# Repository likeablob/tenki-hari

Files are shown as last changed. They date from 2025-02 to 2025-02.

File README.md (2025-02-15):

<div align="center">
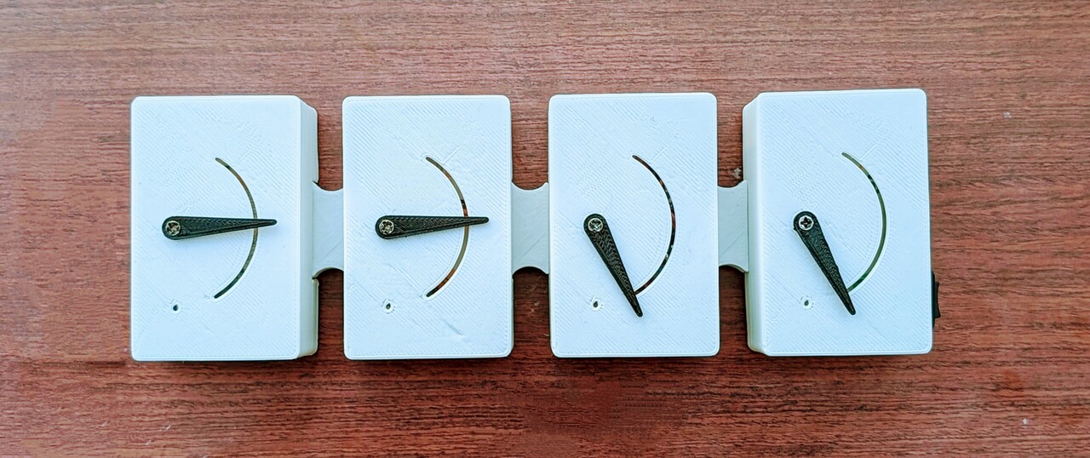
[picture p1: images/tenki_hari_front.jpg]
  
</div>

# Tenki Hari (Weather Needles, *ja: 天気針*)

A minimal weather forecast display gadget – and an experiment in building a battery-powered IoT device with [ESPHome](https://esphome.io/).

## Intro: How I Learned to Stop Worrying and Love ESPHome

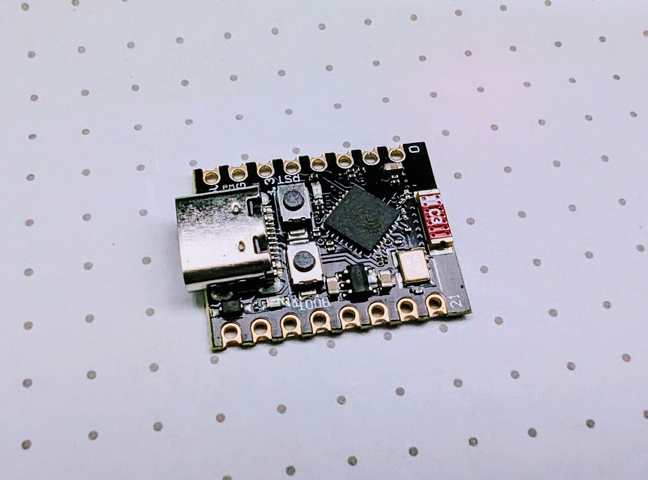
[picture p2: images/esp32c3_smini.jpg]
ESP32-C3 Super Mini


Building home IoT gadgets with embedded programming is fun. However, keeping track of devices scattered around the house ("What *was* that hostname?"), managing over-the-air software updates, and integrating with Home Assistant... not so much.

That's where ESPHome comes in. Think of it as Ansible or Kubernetes for ESP microcontrollers (beware, there's a lot of explicit YAML contents ahead).  It's somewhat similar to [Tasmota](https://tasmota.github.io/docs/), but in my experience, Tasmota is more focused on being an alternative firmware for ESP-based IoT devices.  
ESPHome, while it can certainly be used that way, really shines when it comes to customization.

Here's what I like about ESPHome:

- **Multiple flashing methods supported:** USB, Web Serial!, OTA, via Web UI, and even a full-featured **CLI**.
  - You can even see `ESP_LOGD()` logs over the air.
- **YAML-based device definitions:** (Yes, it's a paved road to YAML HELL.  Keep it simple, stupid!)
  - Secret management using `include` YAMLs (about as good as a `.gitignore`-ed `config.h`).
  - Config validation and autocompletion, thanks to the defined schema.
- **Simple device management dashboard::** Again, CLI is supported, meaning it works headless.
- **Automatic Home Assistant integration:** Devices are auto-detected with HA entities.
- **Extensive peripheral/external device support:** e.g., SPI/I2C sensors, etc.

For example, add this to your device's YAML and flash:

```sh
switch:
  - platform: gpio
    name: "Charge Port 1"
    pin: GPIO4
    restore_mode: RESTORE_DEFAULT_ON
```

Voila! Before you can even finish sipping your coffee, a switch entity appears in your Home Assistant instance.



Sure, it takes away some of the coding fun. However, you can still inject C++ snippets using the [`lambda:` syntax](https://esphome.io/cookbook/lambda_magic.html).  Black magic?  Maybe.  ESPHome is also can be considered as a wrapper that generates Arduino or esp-idf based firmware from your YAML definitions.

## Installation (Quick Overview)

The official ESPHome [Getting Started](https://esphome.io/guides/getting_started_command_line) guide covers installation, but in my case, it was as simple as adding 10 lines to my Home Assistant `docker-compose.yaml`:

```yaml
  esphome:
    container_name: esphome
    image: ghcr.io/esphome/esphome:2024.12.4
    volumes:
      - ./esphome/config:/config
      - /etc/localtime:/etc/localtime:ro
    restart: always
    privileged: true
    network_mode: host # For mDNS
    env_file:
      - esphome.env # This contains `USERNAME` and `PASSWORD`
```

Then, just navigated to http://localhost:6052, clicked `NEW DEVICE`, and followed the wizard. ESPHome creates a `<device-name>.yaml` file to your local filesystem, which you can edit via the dashboard and update via `Install > Wirelessly`.

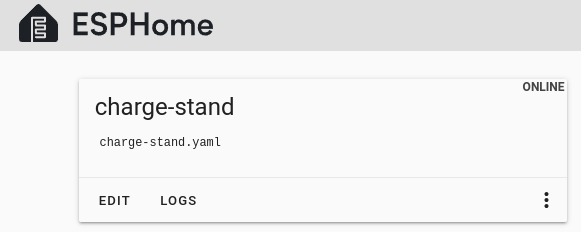
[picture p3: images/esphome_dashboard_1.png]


With this setup, you also need to register the device with Home Assistant for the first time.  When the device is discovered in "Integrations," copy and paste the API key from ESPHome.

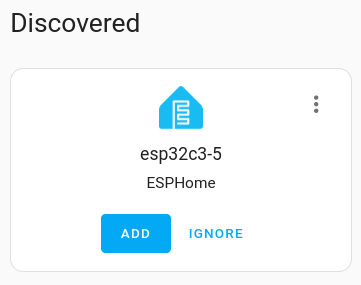
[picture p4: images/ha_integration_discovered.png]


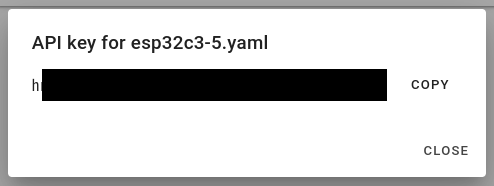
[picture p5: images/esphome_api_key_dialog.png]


One quick note: for initial flashing via the dashboard (using Web Serial), you'll need `localhost` or `https://`. SSH port forwarding (`-L 6052:localhost:6052`) to your home lab server, or you can set up HTTPS with Caddy or Tailscale.  Alternatively, use the [ESPHome Flasher](https://web.esphome.io/) or the CLI (`docker compose exec esphome`).

### Building a Battery-Powered Device with ESPHome

I've built several battery-powered devices in the past, primarily using Arduino ([1](https://github.com/likeablob/slow-movie-player-7c), [2](https://hackaday.io/project/184009-endless-endless-eight)).  Could I build something similar with ESPHome? (Spoiler: Yes!)

Here's the goal:

- An ESP32-C3 powered by 4 x NiMH AA batteries, lasting for *at least* 6 months.
- Wakes up hourly, retrieves the weather forecast for a few hours ahead, and moves a servo to indicate the conditions.
- Wakes up at *specific* times (not just periodically), like 5 minutes past the hour, every hour (`5 * * * *`).

```mermaid
gantt
    dateFormat  HH:mm
    axisFormat  %H:%M
    title       Device sleep and wake schedule

    section Home Assistant
        Fetch weather forecast : milestone, m1, 01:00, 1m
        Fetch weather forecast : milestone, m2, 02:00, 1m
        Fetch weather forecast : milestone, m2, 03:00, 1m

    section Device
        Boot       : milestone, crit, w1, 00:55, 0.2m
        Sleep      : done, after w1, 10m
        Wake       : crit, w2, 01:05, 0.2m
        Sleep      : done, after w2, 59.8m
        Wake       : crit, w3, 02:05, 0.2m
        Sleep      : done, after w3, 59.8m
```

First, [deep sleep is supported](https://esphome.io/components/deep_sleep).  However, by default, ESPHome [provides an API on the device itself](https://esphome.io/components/api) (meaning Home Assistant acts as the client). [Here is why.](https://esphome.io/components/api#advantages-over-mqtt)  Normally, this approach offers low latency, but there's a delay between waking from deep sleep and being recognized by Home Assistant (due to a 60-second polling interval for offline devices ).

Fortunately, [MQTT is also an option](https://esphome.io/components/mqtt.html). Just add this to the top of your YAML:

```yaml
mqtt:
  broker: !secret mqtt_broker
  username: !secret mqtt_username
  password: !secret mqtt_password
  discovery: true
  discovery_prefix: homeassistant
```

Home Assistant will automatically discover the device through the MQTT integration (via the `*/config` topic).  
To receive data, you just need to define the topic and action using `on_message`:

```yaml
mqtt:
  ...
  on_message:
    - topic: home/homeassistant/weather/forecast/3h/condition
      qos: 0
      then:
         ...
```

I use a Home Assistant "Automation" to publish weather forecast data to MQTT topics every hour (with the "Retain" flag set). (See: [Automation Template](./ha_automation_publish_forecast_mqtt.yaml))  
The device subscribes on wake-up and gets the retained data immediately.

### Hitting the Hay Again

How do we let the device wake up from deep sleep periodically? And then let it take a nap for almost an hour.

This is where `deep_sleep`, `mqtt`, and `time` components work together.  
First, define the `deep_sleep` component.  

```yaml
deep_sleep:
  id: deep_sleep_1
  run_duration:
    default: 20s
    gpio_wakeup_reason: 5min
  sleep_duration: 30min
  wakeup_pin:
    number: GPIO4
```

`run_duration` is the *maximum* time the device stays awake. We'll force it to sleep sooner, once it's done its work. `gpio_wakeup_reason` lets us use a shorter `run_duration` if we wake up via the `wakeup_pin` (handy for OTA updates – more on that later).   
If all you need is a simple periodic wake-up (every 30 minutes, say), you can just use `sleep_duration` directly.

To wake up at HH:05, we calculate the time difference between now and the next 5-minutes-past-the-hour mark, and sleep for that duration. The `time` component gives us the current time. Of course, DNS resolution time can be reduced to save on our limited wake-time budget, but let's keep it simple with `0.pool.ntp.org`:

```yaml
time:
  - platform: sntp
    id: sntp_time
    timezone: Etc/UTC
    servers:
      - 0.pool.ntp.org
      - 1.pool.ntp.org
      - 2.pool.ntp.org
```

If you just wanted to wake up at a fixed time each day (e.g., 6 AM), you could use [`until:`](https://esphome.io/components/deep_sleep.html).  But, as of now, [`until:` isn't templatable](https://github.com/esphome/feature-requests/issues/2532) (means no `lambda:` allowed), so we'll do the calculation ourselves.

On wake-up, the device connects to Wi-Fi (DHCP request included), syncs time via SNTP, connects to MQTT, and subscribes. Because the Home Assistant automation publishes *retained* messages, the device receives them immediately.   

We have four servos (for 3h/6h/9h/12h forecasts), so we're using four MQTT topics. That means four `on_message` handlers. We need to sleep *after* receiving all of them.

```yaml
  on_message:
    - topic: home/homeassistant/weather/forecast/3h/condition
      qos: 0
      then:
        - lambda: |-
            ESP_LOGD("main", "Received value is %s", x.c_str());
...
    - topic: home/homeassistant/weather/forecast/6h/condition
      qos: 0
      then:
...
    - topic: home/homeassistant/weather/forecast/9h/condition
      qos: 0
      then:
...
    - topic: home/homeassistant/weather/forecast/12h/condition
      qos: 0
      then:
...
```

For this, we'll use the `script` component. It's for reusable logic, and we can write it in the very similar manner to Home Assistant scripts.

This is the heart of the operation.  It might look a bit long, but it's fairly straightforward:

1.  Increment `received_count` (using `lambda:`). We'll add servo control logic here later.
2.  If `received_count` is 4 (all messages received), start the sleep process.
3.  Power up the servos (via a high-side FET switch) and wait for them to move.
4.  Wait for SNTP time synchronization to complete.
5.  Calculate the sleep duration (in milliseconds) and call `deep_sleep.enter`.
6.  Done!

```yaml
script:
  - id: set_servo_angle
    mode: queued
    then:
    # 1. Increment the counter
      - lambda: |-
          // Implement the servo control logic here
          id(received_count)++;
    # 2. Check if all messages are received
      - if:
          condition:
            lambda: |-
              return id(received_count) >= 4;
          then:
            - logger.log: "The data has been collected. It's time to sleep!"
    # 3. Power up servos and wait
            - output.turn_on: bus_power_switch
            - delay: 1s # Wait for the servo to settle.
    # 4. Wait for time sync
            - wait_until:
                lambda: |-
                  ESP_LOGD("main", "Waiting for time sync: %d", id(sntp_time).now().is_valid());
                  return id(sntp_time).now().is_valid();
    # 5. Calculate sleep duration and go to sleep
            - deep_sleep.enter:
                id: deep_sleep_1
                sleep_duration: !lambda |-
                  auto now = id(sntp_time).now().timestamp;
                  auto next = (now / 3600 + 1) * 3600 + 60 * 5; // Every hour on the 5th minute
                  auto diff_sec = (next - now);
                  ESP_LOGD("main", "Sleep for %ld sec", diff_sec);

                  return diff_sec * 1000; // Return in ms
          else:
            - lambda: |-
                ESP_LOGD("main", "Data collection is in progress.");
```

### Remaining Details

What exactly is `id(received_count)`?  It's a [global variable](https://esphome.io/components/globals.html) (please don't punch me! necessary evil..). Variables can also be stored in RTC memory, so you can create things like `total_boot_count`. Here we simply initialize it on each boot. ESPHome replaces `id(received_count)` with the actual variable name inside the lambda.

```yaml
globals:
  - id: received_count
    type: int
    restore_value: no
    initial_value: "0"
```

For OTA updates, we want to prevent sleep while the external switch is on.  Add this to the script:

```yaml
            - while:
                condition:
                  lambda: |-
                    ESP_LOGD("main", "Waking up while the deep sleep pin is high.");
                    return digitalRead(4) == 1;
                then:
                  - delay: 500ms
```

Let's also track uptime:

```yaml
sensor:
  - platform: template
    id: uptime_millis
    name: "Uptime (millis)"
    accuracy_decimals: 0
```

And just before the sleep logic:

```yaml
            - sensor.template.publish:
                id: uptime_millis
                state: !lambda "return millis();"
```

Servos are defined with `servo` and `output`. We're using the `ledc` peripheral instead of software PWM. (Nice!)

```yaml
output:
  - platform: ledc
    id: pwm_out_1
    pin: GPIO5
    frequency: 50Hz

servo:
  - id: servo_1
    output: pwm_out_1
```

The script also handles moving the servos based on the weather: up for sunny, down for rainy. (Sry, the code is a bit messy.)   
You could also reflect the probability of precipitation.

```yaml
script:
  - id: set_servo_angle
    mode: queued
    parameters:
      servo_ind: int
      weather_condition: string
    then:
      - lambda: |-
          float angle =  0;

          if(weather_condition.find("rainy") != std::string::npos
              || weather_condition == "hail"
              || weather_condition == "pouring"
              || weather_condition.find("snowy") != std::string::npos){
            angle = 150;
          } else if (weather_condition.find("cloudy") != std::string::npos){
            angle = 90;
          } else {
            angle = 30;
          }

          float servo_angle = (90.0f - angle)/90.0f; // 1.0 to -1.0

          switch (servo_ind){
            case 1:
              id(servo_1).write(servo_angle);
              break;
            case 2:
              id(servo_2).write(servo_angle);
              break;
            case 3:
              id(servo_3).write(servo_angle);
              break;
            case 4:
              id(servo_4).write(servo_angle);
              break;
          }

          id(received_count)++;
```

Finally, call the script from the `on_message` handlers:

```yaml
mqtt:
...
  on_message:
    - topic: home/homeassistant/weather/forecast/3h/condition
      qos: 0
      then:
        - lambda: |-
            ESP_LOGD("main", "Received value is %s", x.c_str());
            id(set_servo_angle).execute(1, x);
... # Define other three servos
```

And the GPIO for the bus power switch:

```yaml
output:
...
  - platform: gpio
    pin: GPIO3
    id: bus_power_switch
```

Now we have something that works!  The complete YAML is in [`./esphome_tenki_hari.yaml`](./esphome_tenki_hari.yaml). 

(I've skipped a few minor components here:
- A `number` component to manually control the servos from Home Assistant.
- A `sensor` component to report the wake-up cause.)

### Hardware

- See the [BOM](#bom) for details.
- I de-soldered the power LED from the ESP32-C3 Super Mini board to reduce power consumption.

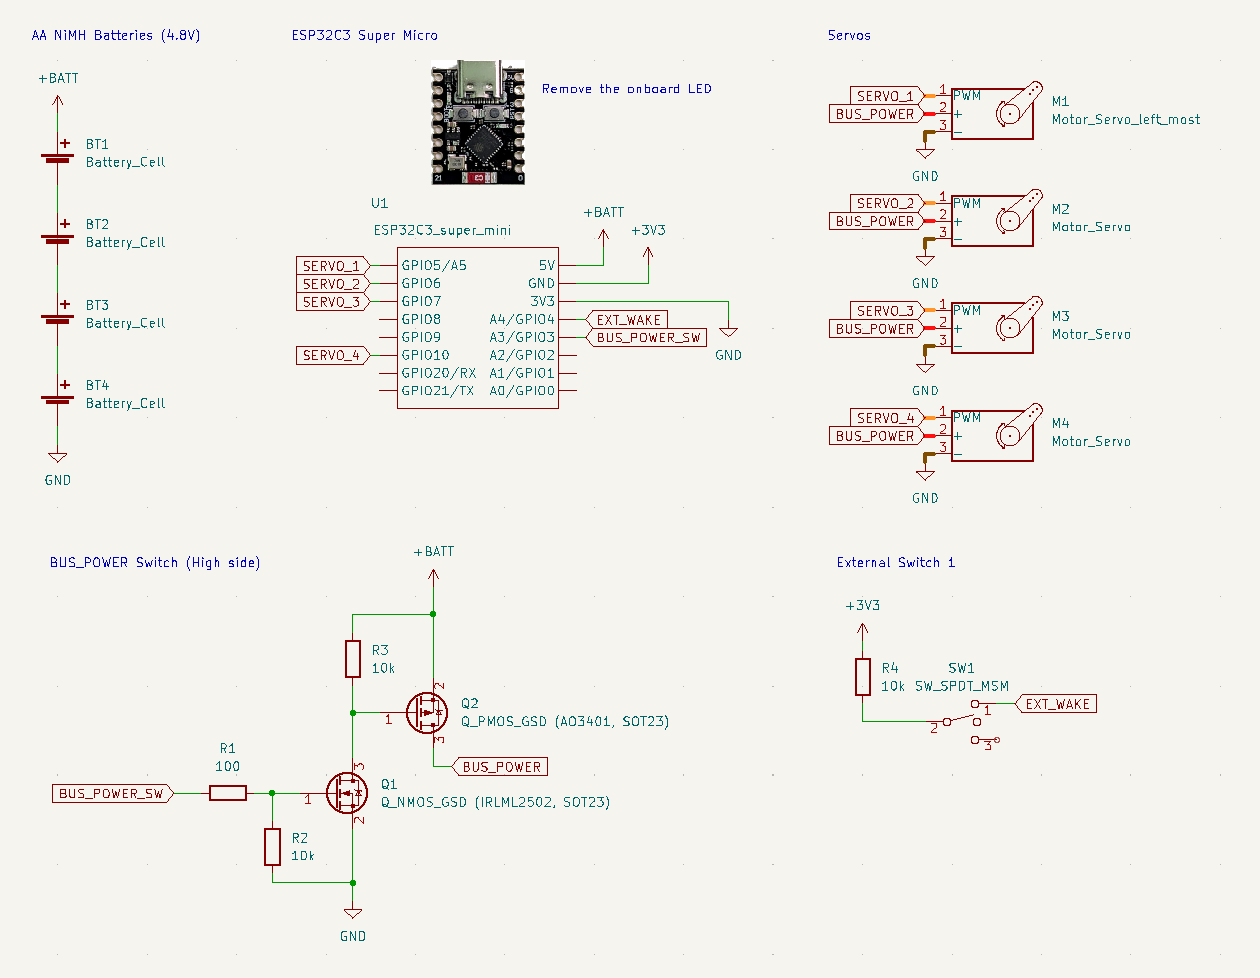
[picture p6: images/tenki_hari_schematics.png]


Solder everything together. Finally, secure, contain, protect this tiny spaghetti monster into the [case](#printable-parts).

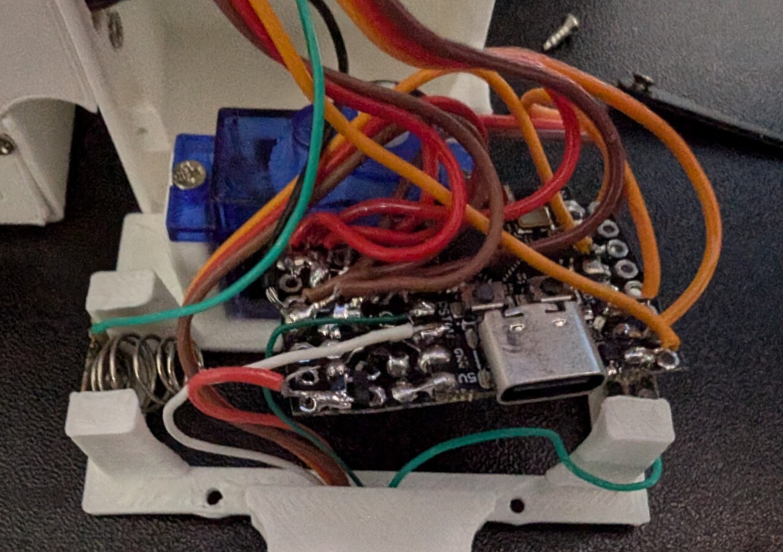
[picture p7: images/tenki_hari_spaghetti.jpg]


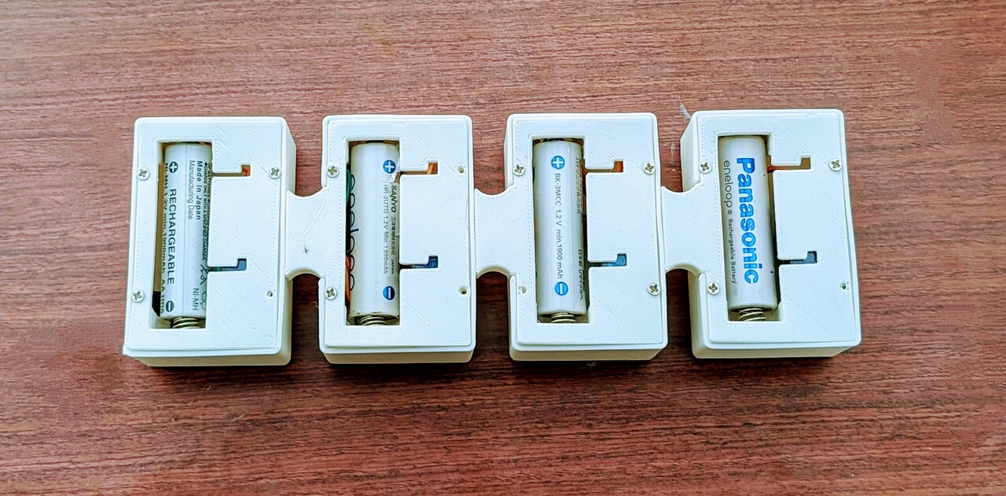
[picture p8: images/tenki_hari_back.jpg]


### Measurements

Here are some numbers about the power consumption(measured with a DMM, @4.8V):

- Power consumption (during boot): ~90 mA
- Power consumption (during sleep): ~110 uA
- Average boot time (from `uptime_millis`): 4.9 s

<a href="https://blc.vercel.app/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">
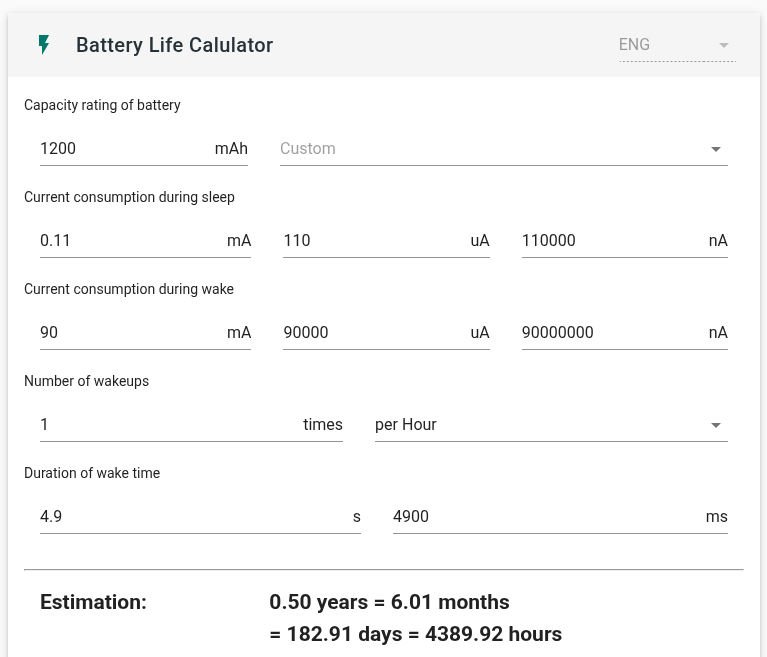
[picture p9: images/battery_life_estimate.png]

</a>

It should last for about six months.  There's also room to shorten the boot time, for example, by using a static IP address.  
So far, the device has been running for several months.

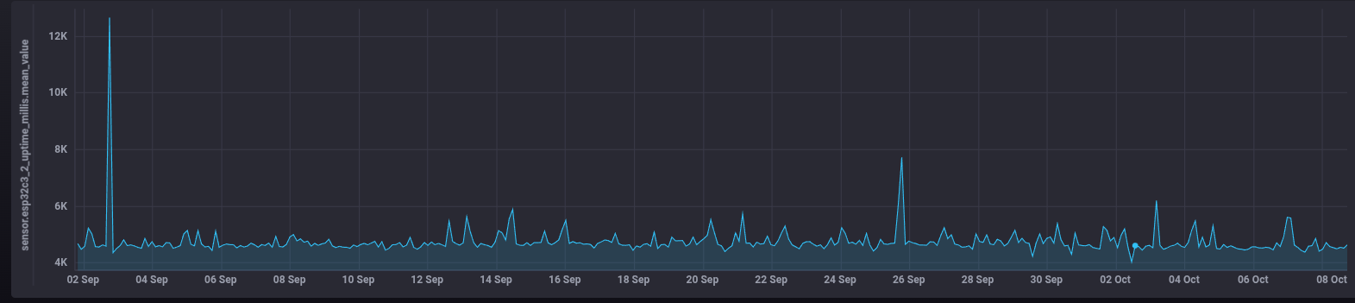
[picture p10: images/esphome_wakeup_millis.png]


### Final Thoughts

- I'm an ESPHome noob, so I may not be writing this in the best way. If you have any suggestions, please let me know!
- ESPHome is a incredibly flexible platform for building all sorts of cool projects. Huge thanks to the ESPHome dev team & community!

## Schematics

See [`./kicad/tenki_hari.kicad_sch`](./kicad/tenki_hari.kicad_sch)

## Printable parts

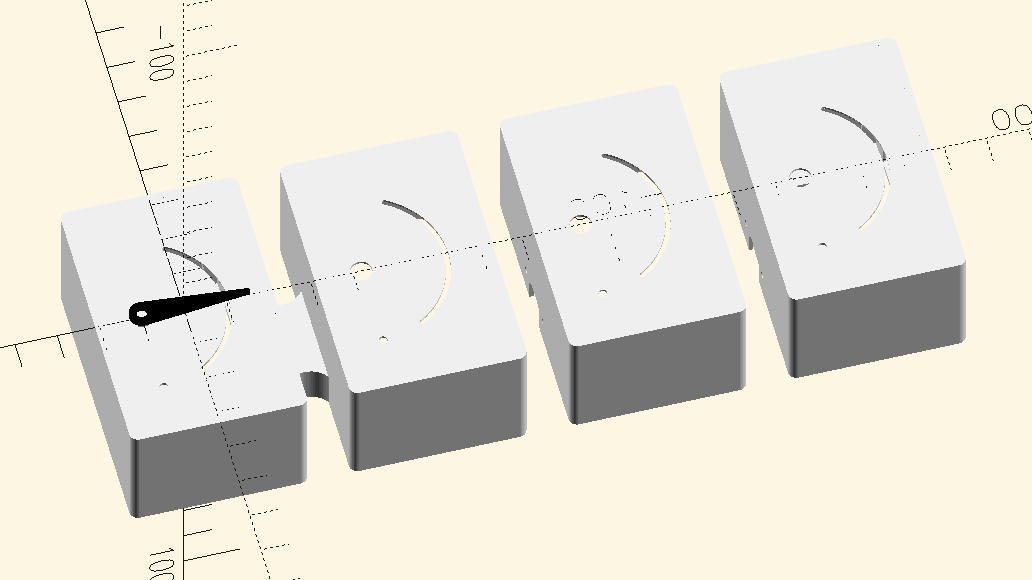
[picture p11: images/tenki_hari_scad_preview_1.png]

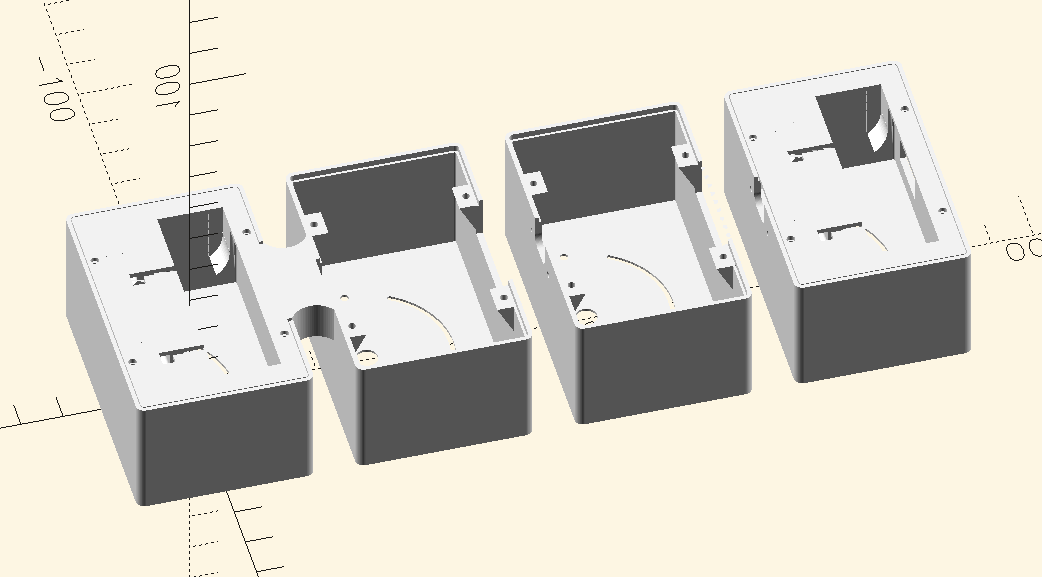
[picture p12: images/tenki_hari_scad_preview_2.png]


| | STL | Quantity |
| --- | --- | :---: |
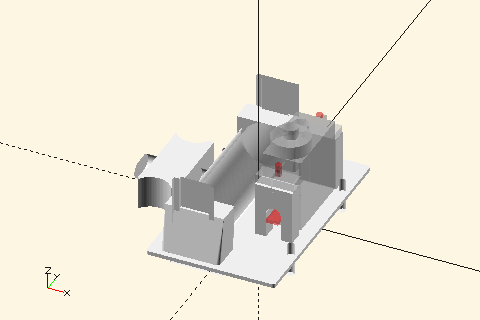
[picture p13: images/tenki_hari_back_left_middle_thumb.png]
|  | [tenki_hari_back_left_middle.stl](./tenki_hari_back_left_middle.stl) | 3 |
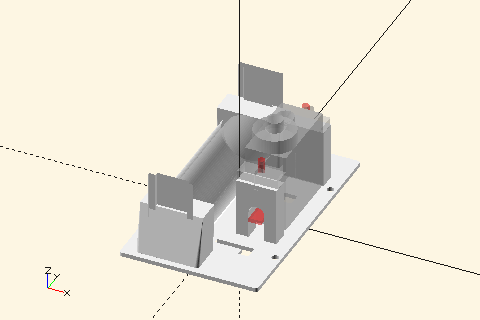
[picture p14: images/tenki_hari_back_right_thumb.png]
|  | [tenki_hari_back_right.stl](./tenki_hari_back_right.stl) | 1 |
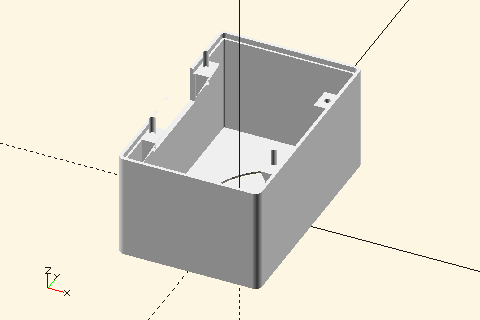
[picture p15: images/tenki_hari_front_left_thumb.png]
|  | [tenki_hari_front_left.stl](./tenki_hari_front_left.stl) | 1 |
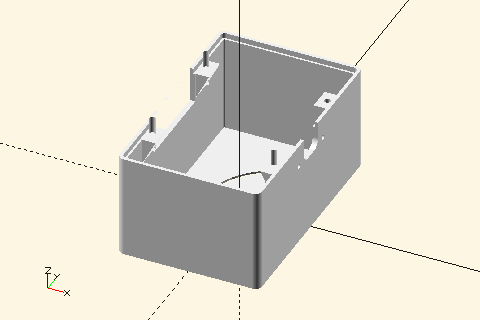
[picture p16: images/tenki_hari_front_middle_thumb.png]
|  | [tenki_hari_front_middle.stl](./tenki_hari_front_middle.stl) | 2 |
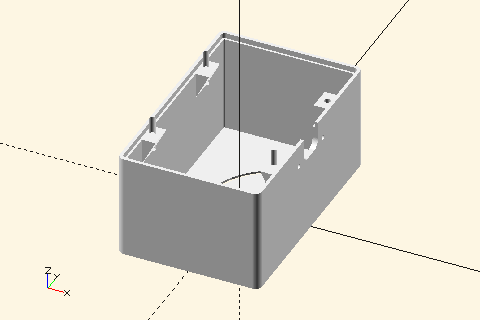
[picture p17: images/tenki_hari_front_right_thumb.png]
|  | [tenki_hari_front_right.stl](./tenki_hari_front_right.stl) | 1 |
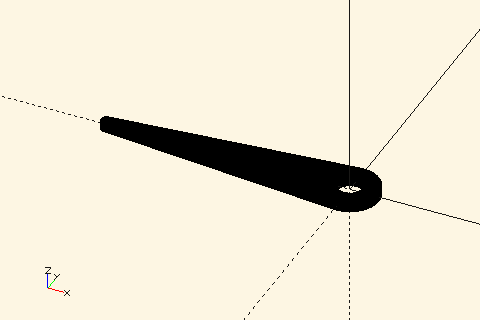
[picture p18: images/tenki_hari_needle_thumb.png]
|  | [tenki_hari_needle.stl](./tenki_hari_needle.stl) | 4 |

```sh
# Generate .stl files from .scad files
$ make all
```

## BOM

| Item | Quantity | Remarks |
| :---: | :---: | --- |
|  ESP32-C3 Super Mini board  | 1 | |
| SG90 servo | 4 | |
| NiMH AA Battery | 4 | |
|  AA Battery contacts pair | 4 | |
| N-MOSFET (IRLML2502, SOT23) | 1 | |
| N-MOSFET (IRLML2502, SOT23) | 1 | |
| 1208 10k SMD Resister | 3 | Can be 100k |
| 1208 100 SMD Resister | 1 | Can be omitted |
| M2 4 mm self tapping screws | 4 | |
| M2 6 mm self tapping screws | 24 | |
| 14 x 9 mm rocker switch | 1 | |

## TODO

- [ ] Profiling and optimization of processing time

## LICENSE

MIT

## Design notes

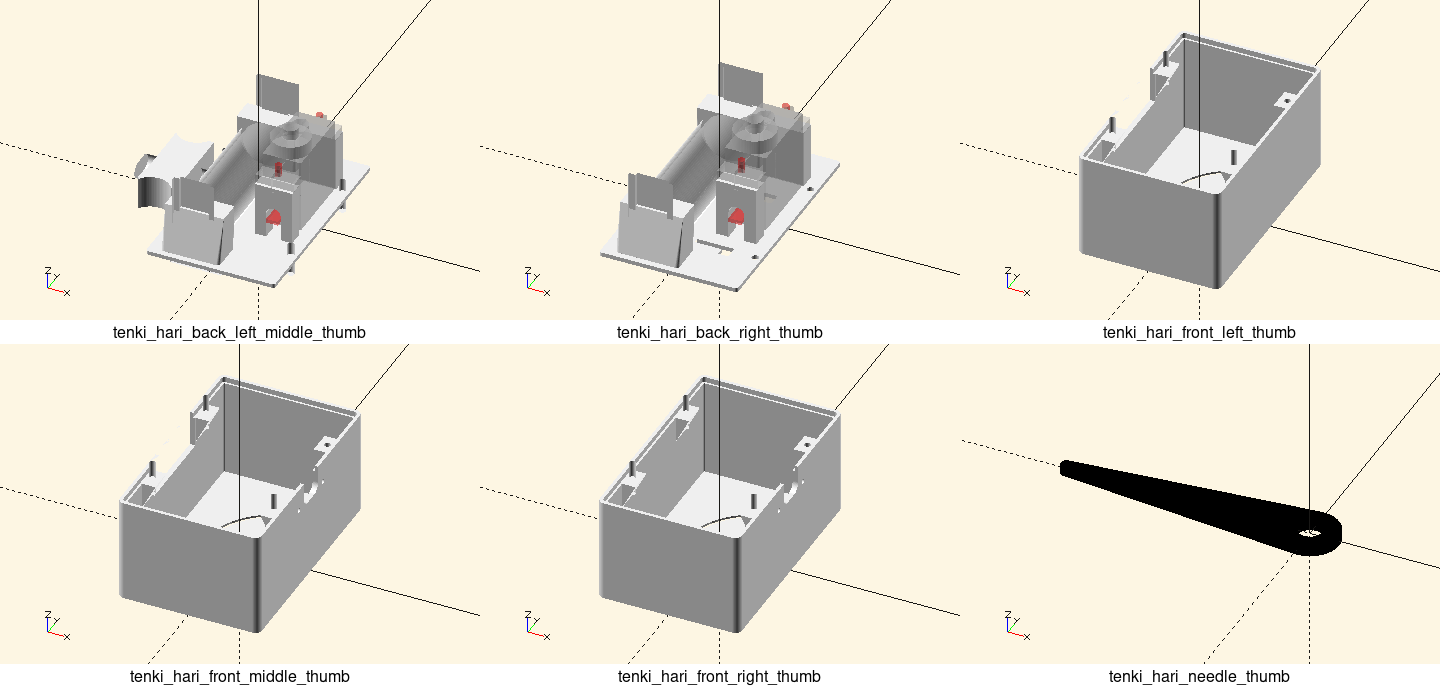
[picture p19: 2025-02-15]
images/models.png

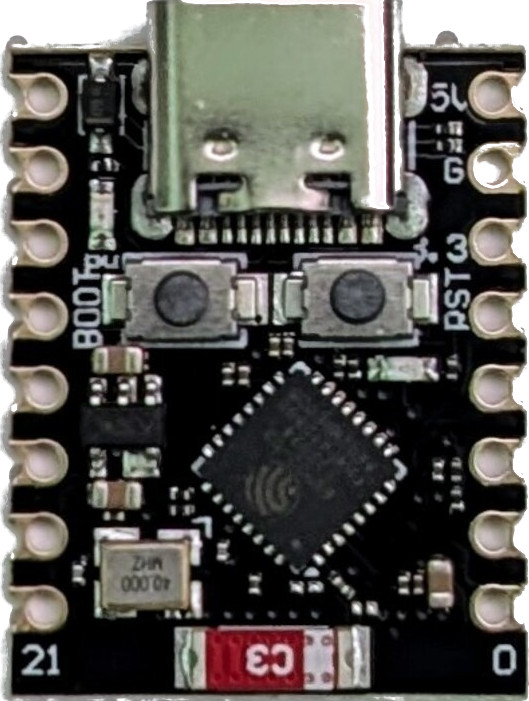
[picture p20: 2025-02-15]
images/esp32c3_smini_2.jpg

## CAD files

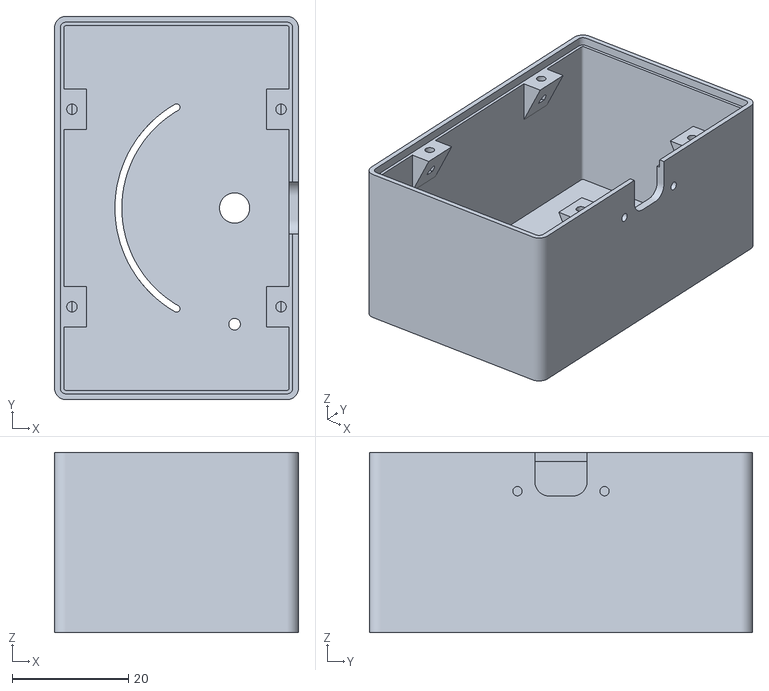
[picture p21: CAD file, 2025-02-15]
tenki_hari_front_right.stl
42.0 x 66.0 x 31.0

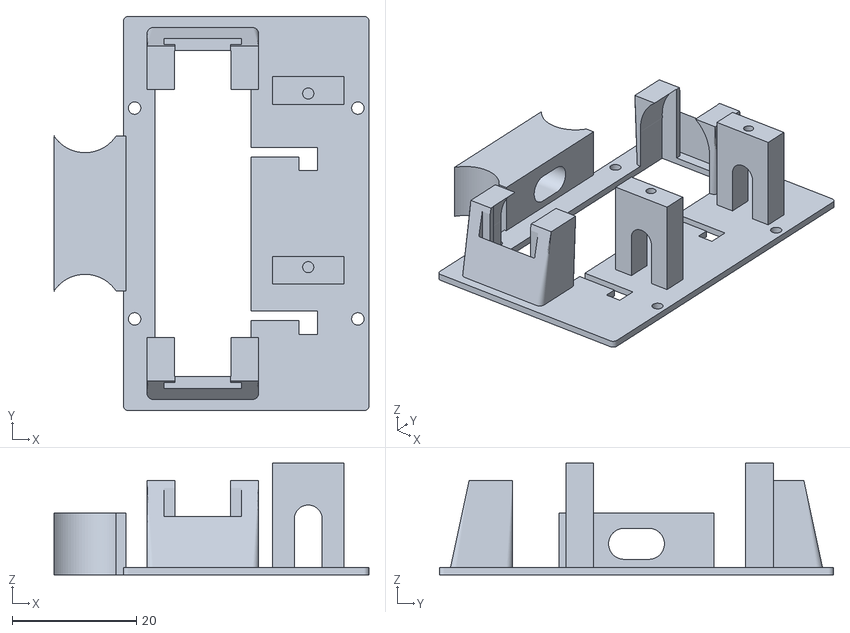
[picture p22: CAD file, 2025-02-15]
tenki_hari_back_left_middle.stl
50.8 x 63.6 x 18.0

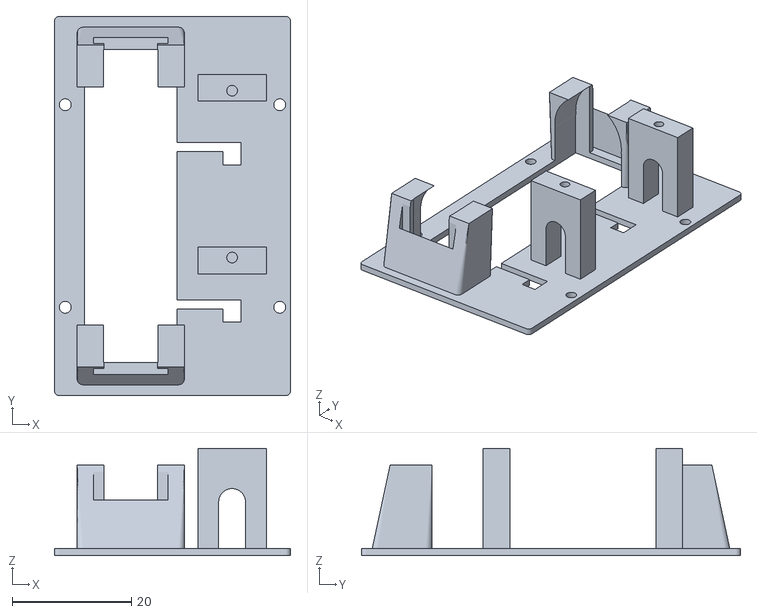
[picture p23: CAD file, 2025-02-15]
tenki_hari_back_right.stl
39.6 x 63.6 x 18.0

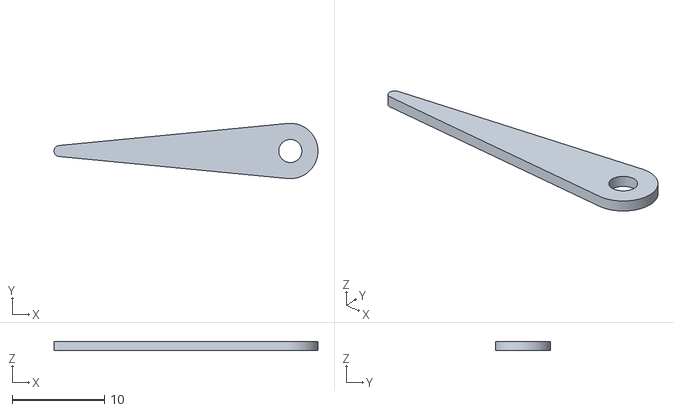
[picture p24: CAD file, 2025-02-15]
tenki_hari_needle.stl
28.6 x 6.00 x 1.00

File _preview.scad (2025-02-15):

include <_tenki_hari_base.scad>

$fn = 80;

// front left
color("#EEE") th_parts_front(prev_side_joint = false);

// back left
color("#EEE") th_parts_back(next_side_joint = true);

// needle
color("#000") translate([ 10, 0, -1.5 ]) th_needle();

// front middle
translate([ -(TH_BODY_SIZE.x + 10), 0, 0 ]) color("#EEE") th_parts_front();

// front middle
translate([ -(TH_BODY_SIZE.x + 10) * 2, 0, 0 ]) color("#EEE") th_parts_front();

// front right
translate([ -(TH_BODY_SIZE.x + 10) * 3, 0, 0 ]) color("#EEE") color("#EEE")
    th_parts_front(rocker_switch = true, next_side_joint = false);

// back right
translate([ -(TH_BODY_SIZE.x + 10) * 3, 0, 0 ]) color("#EEE") color("#EEE")
    th_parts_back(next_side_joint = false);

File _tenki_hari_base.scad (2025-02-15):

include <MCAD/servos.scad>
include <scad-utils/morphology.scad>

$fn = 60;

TH_BODY_SIZE = [ 42, 66, 31 ];
TH_BODY_R = 2;
TH_FACE_THICKNESS = 0.6;
TH_SHELL_THICKNESS = 1.6;

TH_BACKPANEL_THICKNESS = 1.2;

TH_JOINT_SIZE = [ 10, 25, 10 ];

aa_battery_size = [ 14, 50 ];
holder_base_size = [ aa_battery_size.x + 4, 10, aa_battery_size.x ];
holder_base_top = 7;
holder_base_y_offset = 2.5;

*translate([ -4, 0, 14 / 2 + 4 ]) rotate([ 90, 0, 0 ])
    cylinder(d = 14, h = 51, center = true);

module th_base_shape() {
  rounding(r = TH_BODY_R)
      square(size = [ TH_BODY_SIZE.x, TH_BODY_SIZE.y ], center = true);
}

module th_face() {
  difference() {
    th_base_shape();

    // hole for the clock hand
    translate([ 10, 0, 0 ]) circle(d = 5.2);

    // icons
    icons_r = TH_BODY_SIZE.x / 2 + 1;
    icons_deg = [ 60, 0, -60 ];
    icons_files = [ "brightness.svg", "cloud-fill.svg", "umbrella-fill.svg" ];

    *for (i = [0:2]) {
      translate([
        TH_BODY_SIZE.x / 4 - cos(icons_deg[i]) * icons_r,
        sin(icons_deg[i]) * icons_r, 0
      ]) resize([ 18, 0, 0 ], auto = true)
          import(file = icons_files[i], center = true, dpi = 96);
    }

    gauge_arc_r = 20;

    // gauge
    translate([ 10, 0, 0 ]) {
      // arc
      for (i = [-60:60]) {
        rotate([ 0, 0, i ]) translate([ -gauge_arc_r, 0, 0 ]) circle(d = 1.2);
      }

      // ticks
      *for (i = [-60:30:60]) {
        hull() {
          rotate([ 0, 0, i ]) translate([ -gauge_arc_r, 0, 0 ]) circle(d = 2);
          // translate([-gauge_arc_r, 0, 0]){
          //   square(size=[0.5, 2], center=true);
          //   // circle(d=1);

          //   translate([-1, 0, 0])
          //   // circle(d=1);
          //   square(size=[0.5, 2], center=true);
          // }
        }
      }

      // dot
      rotate([ 0, 0, 90 ]) translate([ -gauge_arc_r, 0, 0 ]) circle(d = 2);
    }
  }
}

module th_shell_base() {
  color("#EEE") linear_extrude(height = TH_BODY_SIZE.z, center = false,
                               convexity = 10, twist = 0)
      shell(d = -TH_SHELL_THICKNESS, center = false) th_base_shape();
}

module th_shell(top = false, gap = 0.5) {
  x_pos = top ? (TH_BODY_SIZE.x * 1.1 / 2) - TH_BODY_SIZE.x / 2 + TH_BODY_R +
                    gap / 2
              : (-TH_BODY_SIZE.x * 1.1 / 2) - TH_BODY_SIZE.x / 2 + TH_BODY_R -
                    gap / 2;
  z_pos = top ? 0 : TH_FACE_THICKNESS + gap;

  intersection() {
    *translate([ x_pos, 0, TH_BODY_SIZE.z * 1.1 / 2 + z_pos ])
        cube(size = TH_BODY_SIZE * 1.1, center = true);

    th_shell_base();
  }
}

module th_parts_front(rocker_switch = false,
                      next_side_joint = true,
                      prev_side_joint = true) {
  linear_extrude(height = TH_FACE_THICKNESS, center = false, convexity = 10,
                 twist = 0) th_face();

  difference() {
    th_shell(top = true);

    // for lid
    translate([ 0, 0, TH_BODY_SIZE.z - TH_BACKPANEL_THICKNESS - 0.4 ])
        linear_extrude(height = TH_BACKPANEL_THICKNESS * 2, center = !true,
                       convexity = 10, twist = 0)
            inset(d = TH_SHELL_THICKNESS - 0.6) th_base_shape();

    if (next_side_joint) {
      // for lid joint
      translate([
        -TH_BODY_SIZE.x / 2 + TH_SHELL_THICKNESS / 2, 0,
        TH_BODY_SIZE.z - TH_JOINT_SIZE.z - 0.5
      ]) linear_extrude(height = TH_JOINT_SIZE.z + 0.5, center = !true,
                        convexity = 10, twist = 0)
          square(size = [ TH_SHELL_THICKNESS * 2, TH_JOINT_SIZE.y + 1.5 ],
                 center = true);
    }

    if (prev_side_joint) {
      // screw holes for left joint
      translate([ TH_BODY_SIZE.x / 2, 0, -TH_JOINT_SIZE.z ])
          translate_lid_plane() mirror_y()
              translate([ 0, TH_JOINT_SIZE.y / 2 - 5, TH_JOINT_SIZE.z / 3 ])
                  rotate([ 0, 90, 0 ]) cylinder(d = 1.6, h = 10, center = true);

      // cable holes for joint
      translate(
          [ TH_BODY_SIZE.x / 2 - TH_JOINT_SIZE.x / 2, 0, -TH_JOINT_SIZE.z ])
          translate_lid_plane() hull() {
        mirror_y() translate([ 0, -2, TH_JOINT_SIZE.z / 2 ])
            rotate([ 0, 90, 0 ])
                cylinder(d = 5, h = TH_JOINT_SIZE.x * 2, center = true);

        mirror_y() translate([ 0, -2, TH_JOINT_SIZE.z ]) rotate([ 0, 90, 0 ])
            cylinder(d = 5, h = TH_JOINT_SIZE.x * 2, center = true);
      }
    }

    if (rocker_switch) {
      // hole for rocker switch
      translate([
        -TH_BODY_SIZE.x / 2, -TH_BODY_SIZE.y / 2 + 14.1 / 2 + 6,
        TH_BODY_SIZE.z / 2 - 6
      ]) cube(size = [ 10, 14.1, 9 ], center = true);
    }
  }

  // screw bases for lid
  pos_lid_screws() translate([ 0, 0, -TH_BACKPANEL_THICKNESS - 0.4 ])
      difference() {
    hull() {
      screw_base_size = [ 5, 7, 10 ];
      linear_extrude(height = 0.01, center = true, convexity = 10, twist = 0)
          square([ screw_base_size.x, screw_base_size.y ], center = true);

      translate([ screw_base_size.x / 2, 0, -screw_base_size.z ])
          linear_extrude(height = 0.01, center = true, convexity = 10,
                         twist = 0)
              square([ 0.01, screw_base_size.y ], center = true);
    }

    // screw holes
    cylinder(d = 1.8, h = 10, center = true);
  }
}

module translate_lid_plane() {
  translate([ 0, 0, TH_BODY_SIZE.z ]) children();
}

SERVO_HOLDER_BASE_SIZE = [ 11.5, 4.5, TH_BODY_SIZE.z - 13 ];
SERVO_SCREW_HOLE_TO_HOLE = 28;

module servo_holder_base() {
  difference() {
    mirror_y() translate([
      0, SERVO_SCREW_HOLE_TO_HOLE / 2 + 0.5, -SERVO_HOLDER_BASE_SIZE.z / 2
    ]) difference() {
      cube(SERVO_HOLDER_BASE_SIZE, center = true);

      // space for cables
      hull() {
        translate([ 0, 0, SERVO_HOLDER_BASE_SIZE.z ]) rotate([ 90, 0, 0 ])
            cylinder(d = 4.5, h = SERVO_HOLDER_BASE_SIZE.y + 1, center = true);

        rotate([ 90, 0, 0 ])
            cylinder(d = 4.5, h = SERVO_HOLDER_BASE_SIZE.y + 1, center = true);
      }
    }

    // screw holes
    mirror_y() translate(
        [ 0, SERVO_SCREW_HOLE_TO_HOLE / 2, -SERVO_HOLDER_BASE_SIZE.z / 2 ])
        cylinder(d = 1.8, h = SERVO_HOLDER_BASE_SIZE.z, center = true);
  }
}

module th_parts_back(next_side_joint = true) {
  if (next_side_joint) {
    // joint
    translate(
        [ -TH_BODY_SIZE.x / 2 - TH_JOINT_SIZE.x / 2, 0, -TH_JOINT_SIZE.z ])
        translate_lid_plane() difference() {
      union() {
        linear_extrude(height = TH_JOINT_SIZE.z, center = !true, convexity = 10,
                       twist = 0) fillet(r = 6) union() {
          mirror_x() translate([ TH_JOINT_SIZE.x / 2, 0, 0 ])
              square(size = [ 0.01, TH_JOINT_SIZE.y ], center = true);
        }

        // lid joint
        translate([ TH_JOINT_SIZE.z / 2 + TH_SHELL_THICKNESS / 2, 0, 0 ])
            linear_extrude(height = TH_JOINT_SIZE.z, center = !true,
                           convexity = 10, twist = 0)
                square(size = [ TH_SHELL_THICKNESS, TH_JOINT_SIZE.y ],
                       center = true);
      }

      // screw holes
      mirror_y() translate([
        -TH_JOINT_SIZE.x / 2, TH_JOINT_SIZE.y / 2 - 5, TH_JOINT_SIZE.z / 3
      ]) rotate([ 0, 90, 0 ]) cylinder(d = 1.6, h = 10, center = true);

      // cable holes
      hull() {
        mirror_y() translate([ 0, -2, TH_JOINT_SIZE.z / 2 ])
            rotate([ 0, 90, 0 ])
                cylinder(d = 5, h = TH_JOINT_SIZE.x * 2, center = true);
      }
    }
  }

  // lid
  difference() {
    translate([ 0, 0, -TH_BACKPANEL_THICKNESS ]) translate_lid_plane()
        linear_extrude(height = TH_BACKPANEL_THICKNESS, center = !true,
                       convexity = 10, twist = 0)
            inset(d = TH_SHELL_THICKNESS - 0.4) th_base_shape();

    // screw holes
    pos_lid_screws() cylinder(d = 2, h = 10, center = true);

    // band holes
    for (i = [ 0, TH_BODY_SIZE.y / 2.5 ]) {
      translate([ 0, (TH_BODY_SIZE.y / 4) - i, 0 ]) translate_lid_plane()
          linear_extrude(height = TH_BACKPANEL_THICKNESS * 2, center = true,
                         convexity = 10, twist = 0) union() {
        BAND_HOLE_SIZE = [ 23, 3, 1.5 ];

        mirror_x() translate([
          BAND_HOLE_SIZE.x / 2 - BAND_HOLE_SIZE[2] * 2 / 2,
          BAND_HOLE_SIZE.y / 2, 0
        ]) square(size = [ BAND_HOLE_SIZE[2] * 2, BAND_HOLE_SIZE.y ],
                  center = true);

        square(size = [ BAND_HOLE_SIZE.x, BAND_HOLE_SIZE[2] ], center = true);
      }
    }

    // space for battery
    translate([ -14 / 2, 0, -TH_BACKPANEL_THICKNESS - 1 ]) translate_lid_plane()
        linear_extrude(height = aa_battery_size.x / 2, center = !true,
                       convexity = 10, twist = 0)
            square(size =
                       [
                         aa_battery_size.x + 1.5, aa_battery_size.y +
                         holder_base_y_offset
                       ],
                   center = true);
  }
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

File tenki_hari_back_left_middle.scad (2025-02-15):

include <_tenki_hari_base.scad>

$fn = 80;
translate_lid_plane() rotate([ 180, 0, 0 ]) {
  color("#EEE") th_parts_back(next_side_joint = true);

  // AA battery
  % aa_battery();

  // SG90 servo
  % servo();
};

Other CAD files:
tenki_hari_front_middle.stl
tenki_hari_front_left.stl
tenki_hari_back_right.scad
tenki_hari_front_left.scad
tenki_hari_front_middle.scad
tenki_hari_front_right.scad
tenki_hari_needle.scad

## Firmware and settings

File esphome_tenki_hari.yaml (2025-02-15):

esphome:
  name: tenki_hari_1
  friendly_name: tenki_hari_1

esp32:
  board: esp32-c3-devkitm-1
  framework:
    type: arduino

# Enable logging
logger:

ota:
  - platform: esphome
    password: "<Replace This>"

wifi:
  ssid: !secret wifi_ssid
  password: !secret wifi_password

  on_connect:
    - logger.log:
        format: "Wake up cause is %d"
        args: ["id(wakeup_cause).state"]

captive_portal:

time:
  - platform: sntp
    id: sntp_time
    timezone: Etc/UTC
    servers:
      - 0.pool.ntp.org
      - 1.pool.ntp.org
      - 2.pool.ntp.org

deep_sleep:
  id: deep_sleep_1
  run_duration:
    default: 20s
    gpio_wakeup_reason: 5min
  sleep_duration: 30min
  wakeup_pin:
    number: GPIO4

globals:
  - id: received_count
    type: int
    restore_value: no
    initial_value: "0"

script:
  - id: set_servo_angle
    mode: queued
    parameters:
      servo_ind: int
      weather_condition: string
    then:
      # Possible conditions: https://www.home-assistant.io/integrations/weather/
      - lambda: |-
          float angle =  0;

          if(weather_condition.find("rainy") != std::string::npos
              || weather_condition == "hail"
              || weather_condition == "pouring"
              || weather_condition.find("snowy") != std::string::npos){
            angle = 150;
          } else if (weather_condition.find("cloudy") != std::string::npos){
            angle = 90;
          } else {
            angle = 30;
          }

          float servo_angle = (90.0f - angle)/90.0f; // 1.0 to -1.0

          switch (servo_ind){
            case 1:
              id(servo_1).write(servo_angle);
              break;
            case 2:
              id(servo_2).write(servo_angle);
              break;
            case 3:
              id(servo_3).write(servo_angle);
              break;
            case 4:
              id(servo_4).write(servo_angle);
              break;
          }

          id(received_count)++;
      - if:
          condition:
            lambda: |-
              return id(received_count) >= 4;
          then:
            - logger.log: "The data has been collected. It's time to sleep!"
            - output.turn_on: bus_power_switch
            - delay: 1s # Wait for the servo to settle.
            - wait_until:
                lambda: |-
                  ESP_LOGD("main", "Waiting for time sync: %d", id(sntp_time).now().is_valid());
                  return id(sntp_time).now().is_valid();
            - while:
                condition:
                  lambda: |-
                    ESP_LOGD("main", "Waking up while the deep sleep pin is high.");
                    return digitalRead(4) == 1;
                then:
                  - delay: 500ms
            - sensor.template.publish:
                id: uptime_millis
                state: !lambda "return millis();"
            # Note: deep_sleep.until is not templatable: https://github.com/esphome/feature-requests/issues/2532
            - deep_sleep.enter:
                id: deep_sleep_1
                sleep_duration: !lambda |-
                  auto now = id(sntp_time).now().timestamp;
                  auto next = (now / 3600 + 1) * 3600 + 60 * 5; // Every hour on the 5th minute
                  auto diff_sec = (next - now);
                  ESP_LOGD("main", "Sleep for %ld sec", diff_sec);

                  return diff_sec * 1000; // Return in ms
          else:
            - lambda: |-
                ESP_LOGD("main", "Data collection is in progress.");

output:
  - platform: ledc
    id: pwm_out_1
    pin: GPIO5
    frequency: 50Hz
  - platform: ledc
    id: pwm_out_2
    pin: GPIO6
    frequency: 50Hz
  - platform: ledc
    id: pwm_out_3
    pin: GPIO7
    frequency: 50Hz
  - platform: ledc
    id: pwm_out_4
    pin: GPIO10
    frequency: 50Hz
  - platform: gpio
    pin: GPIO3
    id: bus_power_switch

servo:
  - id: servo_1
    output: pwm_out_1
  - id: servo_2
    output: pwm_out_2
  - id: servo_3
    output: pwm_out_3
  - id: servo_4
    output: pwm_out_4

sensor:
  - platform: template
    id: wakeup_cause
    name: "Wakeup Cause"
    accuracy_decimals: 0
    lambda: return esp_sleep_get_wakeup_cause();
    internal: False
  - platform: template
    id: uptime_millis
    name: "Uptime (millis)"
    accuracy_decimals: 0
  - platform: template
    id: deep_sleep_gpio
    internal: true
    accuracy_decimals: 0
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
